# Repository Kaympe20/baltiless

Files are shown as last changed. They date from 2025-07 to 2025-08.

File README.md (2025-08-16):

# Baltiless
An antweight combat robot that hates baltimore

---

[As featured on](https://highway.hackclub.com/projects/kaympe20/baltiless)

[](https://highway.hackclub.com/projects/kaympe20/baltiless)

---

I made this project because I love doing robotics, but so many robotics leagues are both prohibitively expensive and require a team. I started on combat robot stuff because I saw a Maker's Muse video on antweight design and I really wanted to experience it myself.

The name and theming are inspired from [this iconic ad](https://www.youtube.com/watch?v=wQVhb4DxHnw)

(https://www.youtube.com/watch?v=wQVhb4DxHnw)

## Pics





## CAD

The entire CAD workspace can be found on [Onshape](https://cad.onshape.com/documents/90a72f74635ef8557d1759b8/w/d9ba49a82c021e2d515db92d/e/680649447d37402c596404bf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)

## BOM

### Required Each Build

| Item | Quantity | Price | Price After Taxes + Shipping |
|---|---|---|---|
| [Malenki-Nano](https://turnabot.com/products/malenki-nano-integrated-6-channel-triple-electronic-speed-controller-receiver-combo) | 1 | $28.00 | $34.30
| [N20 Gearmotor](https://www.aliexpress.us/item/2251832836005412.html) | 2 | $4.46 | $11.58
| [Brushless 2205 Motor - 2300kV](https://www.aliexpress.us/item/3256807958524880.html) | 1 | $7.41 | $8.85
| [AM32 40A Budget ESC with BEC](https://www.aliexpress.us/item/3256807247202971.html) | 1 | $11.38 | $17.65
| [2S 550mAh 7.6V 80C LiPo Battery Pack w/XT30](https://hobbyking.com/en_us/550mah-2s-xt30-80c-lihv.html) | 1 | $6.64 | $13.77
| [XT30 Battery Connector](https://www.aliexpress.us/item/3256806414638022.html) | 1 | $1.69 | $5.22
| [M2 Heat Set Inserts](https://www.amazon.com/ruthex-Threaded-Insert-pieces-ultrasound/dp/B088QJG676) (This brand was shown to be the strongest in [testing by CNC Kitchen](https://youtu.be/G-UF4tv3Hvc?t=518))| 1 | $8.99 | $9.53
| [M5 Female to Female Standoff x 25mm](https://www.digikey.com/en/products/detail/w%C3%BCrth-elektronik/970300581/6174852) | 2 | $1.40 | $6.78

### Required Once

| Item | Quantity | Price | Price After Taxes + Shipping |
|---|---|---|---|
| [Battery Charger](https://www.amazon.com/SUPULSE-Battery-Charger-7-4-11-1V-B3V2/dp/B099K8XFG6) | 1 | $15.99 | $16.95
| [A compatible transmitter](https://docs.google.com/document/d/1de-4Ajfx2jMYSQTj5gIVWLmTVmklHdIL7C0gMfFrDcg/edit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) (I used a [Flysky FS-i6x](https://www.amazon.com/DTXMX-Transmitter-Receiver-Channels-Quadcopter/dp/B0B69B3QCS) (cheaper to get on amazon if you have prime, if not [get it on aliexpress](https://www.aliexpress.us/item/3256808911086039.html))) | 1 | $54.99 | $59.29

Total: $183.92

## Wiring



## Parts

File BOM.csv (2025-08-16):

Category | Item | Link | Quantity | Price | Price After Taxes + Shipping
Required Each Build | Malenki-Nano | https://turnabot.com/products/malenki-nano-integrated-6-channel-triple-electronic-speed-controller-receiver-combo | 1 | $28.00 | $34.30
Required Each Build | N20 Gearmotor | https://www.aliexpress.us/item/2251832836005412.html | 2 | $4.46 | $11.58
Required Each Build | Brushless 2205 Motor - 2300kV | https://www.aliexpress.us/item/3256807958524880.html | 1 | $7.41 | $8.85
Required Each Build | AM32 40A Budget ESC with BEC | https://www.aliexpress.us/item/3256807247202971.html | 1 | $11.38 | $17.65
Required Each Build | 2S 550mAh 7.6V 80C LiPo Battery Pack w/XT30 | https://hobbyking.com/en_us/550mah-2s-xt30-80c-lihv.html | 1 | $6.64 | $13.77
Required Each Build | XT30 Battery Connector | https://www.aliexpress.us/item/3256806414638022.html | 1 | $1.69 | $5.22
Required Each Build | M2 Heat Set Inserts | https://www.amazon.com/ruthex-Threaded-Insert-pieces-ultrasound/dp/B088QJG676 | 1 | $8.99 | $9.53
Required Each Build | M5 Female to Female Standoff x 25mm | https://www.digikey.com/en/products/detail/w%C3%BCrth-elektronik/970300581/6174852 | 2 | $1.40 | $6.78
Required Once | Battery Charger | https://www.amazon.com/SUPULSE-Battery-Charger-7-4-11-1V-B3V2/dp/B099K8XFG6 | 1 | $15.99 | $16.95
Required Once | A compatible transmitter (Flysky FS-i6x) | https://www.amazon.com/DTXMX-Transmitter-Receiver-Channels-Quadcopter/dp/B0B69B3QCS | 1 | $54.99 | $59.29

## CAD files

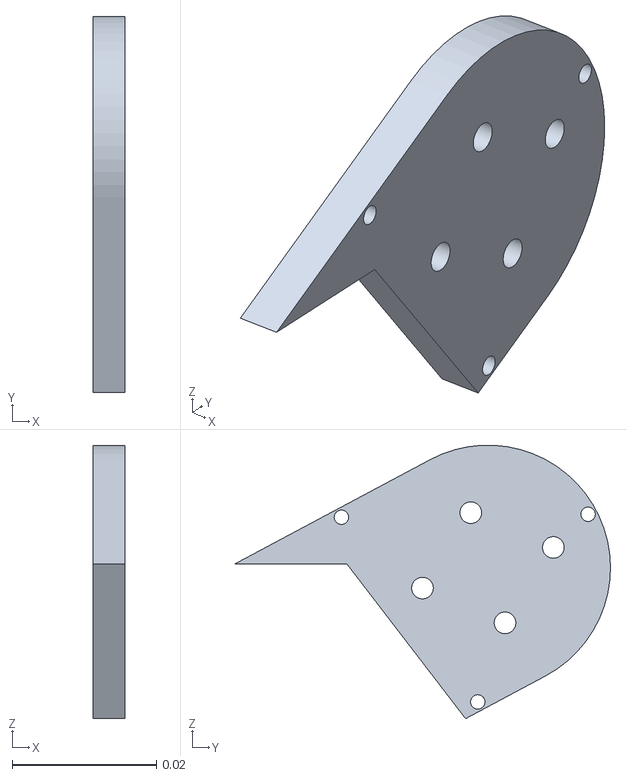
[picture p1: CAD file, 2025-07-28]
Custom Parts/Main Part Studio - Motor Housing Cover.stl
0.0045 x 0.0521 x 0.0379

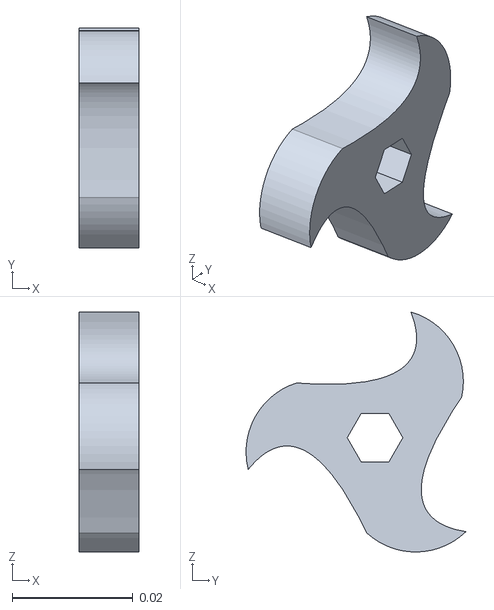
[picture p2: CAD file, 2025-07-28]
Custom Parts/Main Part Studio - Spinner.stl
0.01 x 0.0365 x 0.0398

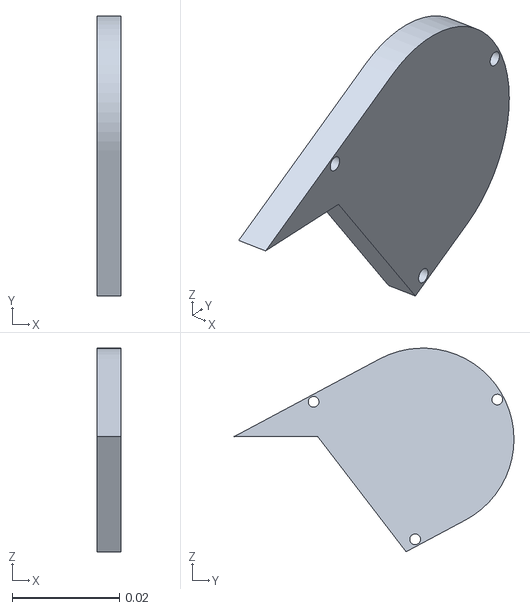
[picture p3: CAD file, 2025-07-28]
Custom Parts/Main Part Studio - Motor Housing Opposite Side.stl
0.0045 x 0.0521 x 0.0379

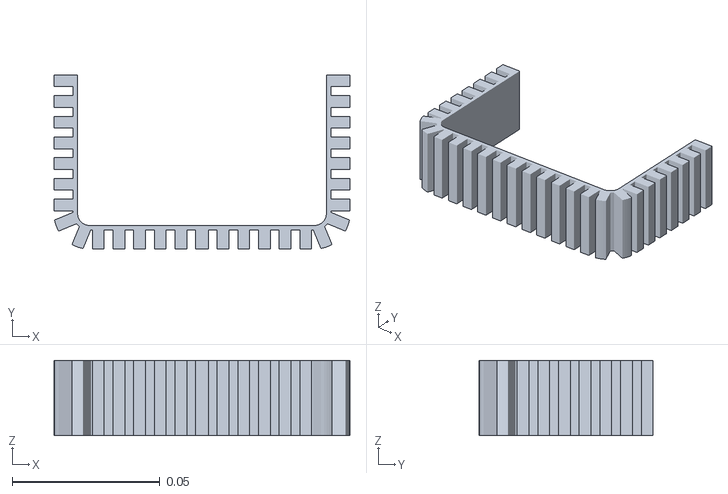
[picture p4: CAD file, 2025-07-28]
Custom Parts/Main Part Studio - TPU Deflector.stl
0.1 x 0.0589 x 0.0254

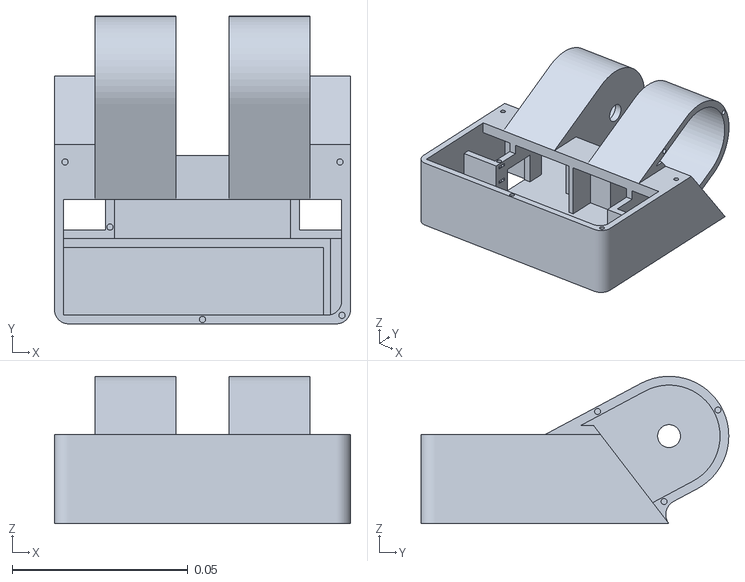
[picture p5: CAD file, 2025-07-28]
Custom Parts/Main Part Studio - Main Body.stl
0.0842 x 0.0875 x 0.0419

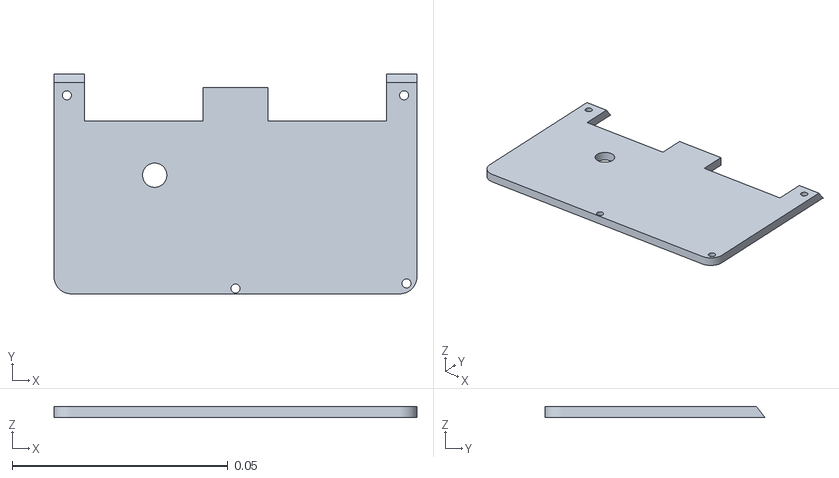
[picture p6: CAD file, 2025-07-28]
Custom Parts/Main Part Studio - Top Plate.stl
0.0842 x 0.0509 x 0.0025

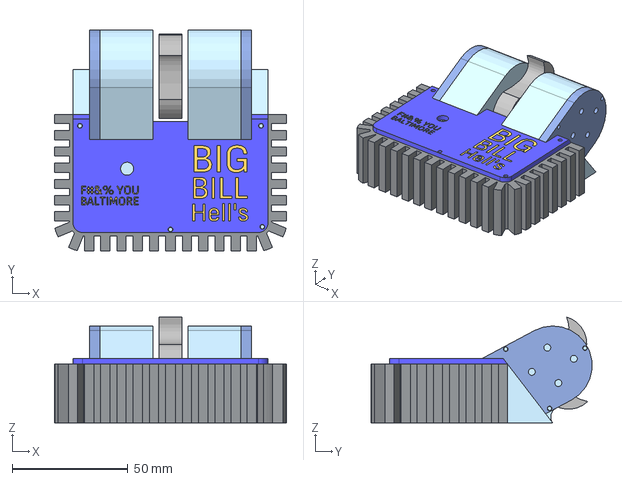
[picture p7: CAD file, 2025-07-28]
All Custom Parts.step
100.2 x 95.4 x 45.8 mm

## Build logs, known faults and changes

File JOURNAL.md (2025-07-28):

---
title: "Baltiless"
author: "Kayla Blosser aka @Kayla"
description: "An antweight combat robot that hates baltimore"
created_at: "2025-07-03"
---

Total Time Spent: 17 hr 10 min

---

## July 6, 2025

I started by watching this YouTube video to try and understand the basics of creating combat robots.

(https://www.youtube.com/watch?v=BvNRtRuOALw)

Time Spent: 30 mins

---

I started researching what **E**lectronic **S**peed **C**ontroller to use and came across the [Malenki-Nano](https://botbitz.com.au/collections/antweight-parts/products/malenki-nano), which combines a lot of the functions I need, reducing weight and allowing enough excess to implement a cool weapon.



Time Spent: 40 mins

---

I got started researching all the parts I would need including a second ESC for a larger motor.



Time Spent: 1.5hrs

--- 

I have begun CAD to make the chassis where all the parts will fit into.



Time Spent: 1hr

---

## July 7, 2025

I am mostly done with the CAD side; there's just a few things I need to do and I should be off to the races.



Time Spent: 4.5hr

---

## July 8, 2025

I improved on the design a lot, including making it a lot stronger, shrinking to allow for TPU deflectors, and moving stuff around to allow for a much bigger weapon.



Next time, I'll get working on the TPU deflectors, actually modelling out the weapon, and other things nessecary to get it competition ready, such as adding a power switch and alan key power switch.

Time Spent: 3.5hr

---

## July 9, 2025

We now have a TPU deflector and a full blade. The deflector was a bit challenging because putting it in required the body to be significantly smaller to still fit within the 4inx4in limit.





The weapon was made to fit this standoff, which I repurposed as a hex-shaped shaft to attach the weapon to the M5 bolt on the motor.

(https://www.digikey.com/en/products/detail/w%C3%BCrth-elektronik/970300581/6174852)



Time Spent: 3hr

---

I added the [FingerTech Mini Power Switch](https://repeat-robotics.com/buy/fingertech-switch/) because it stops a switch from needing to be on the top which could be unintentionally triggered.

Originally, I couldn't find a place to mount it.



But then I realized I could use the little cutouts on the side and add inserts that would allow me to attach it to the left wheel well.







In the bot's full current form, it looks like this:





Time Spent: 1.5hr

---

## July 28, 2025

I made [Logan Peterson](https://github.com/SharKingStudios)'s' requested changes, including uploading the files and adding prices to the BOM. I also heavily optimized the BOM to keep it as cheap as possible, including going for a fully 3D printed weapon (we'll have to see how that one goes).



Time Spent: 1hr

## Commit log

2025-07-07 Add BOM and beginning stages of CAD
2025-07-07 Update CAD
2025-07-09 Add shaft, TPU deflector, and weapon
2025-07-09 Add power switch
2025-07-16 Prepare for submission
    [BOM.csv]
2025-07-28 Add 3D Printed Part Files
    [All Custom Parts.step, Main Part Studio - Main Body.stl, Main Part Studio - Motor Housing Cover.stl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]
2025-07-28 Change BOM as requested
    [BOM.csv]
2025-08-16 Use Aliexpress whereever possible
    [BOM.csv]
